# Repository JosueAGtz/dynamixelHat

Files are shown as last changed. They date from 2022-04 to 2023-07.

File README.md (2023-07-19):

# RaspberryPi Dynamixel Hat

The Raspberry Pi Zero Dynamixel Hat it's an easy to use hardware that allows you to connect and communicate with Dynamixel Servo Motors by using the Savage Electronics AX interface circuit, providing the half-duplex communication needed by these motors, its implemented in it a voltage converter for all the signals to the Raspberry allowing a secure communication in terms of logical levels.

It also implements a MAX25232ATCG/V+ which is a synchronous step-down DC-DC converter optimized for applications with high power density, This regulator will let you power your Raspberry directly from a battery and also provide power to your motors.

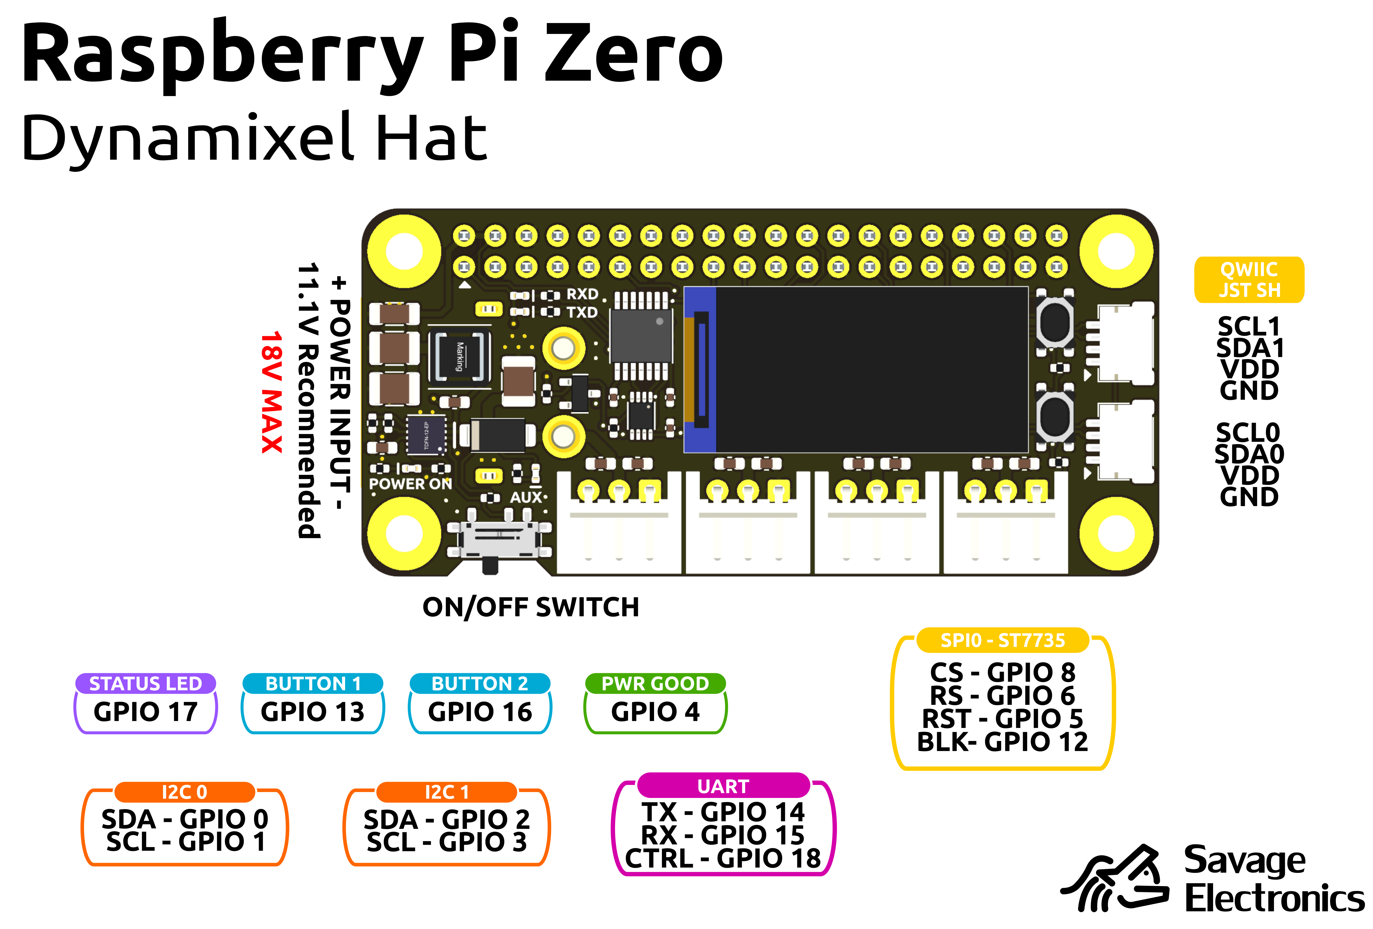
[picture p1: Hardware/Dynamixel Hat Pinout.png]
dynamixelHat


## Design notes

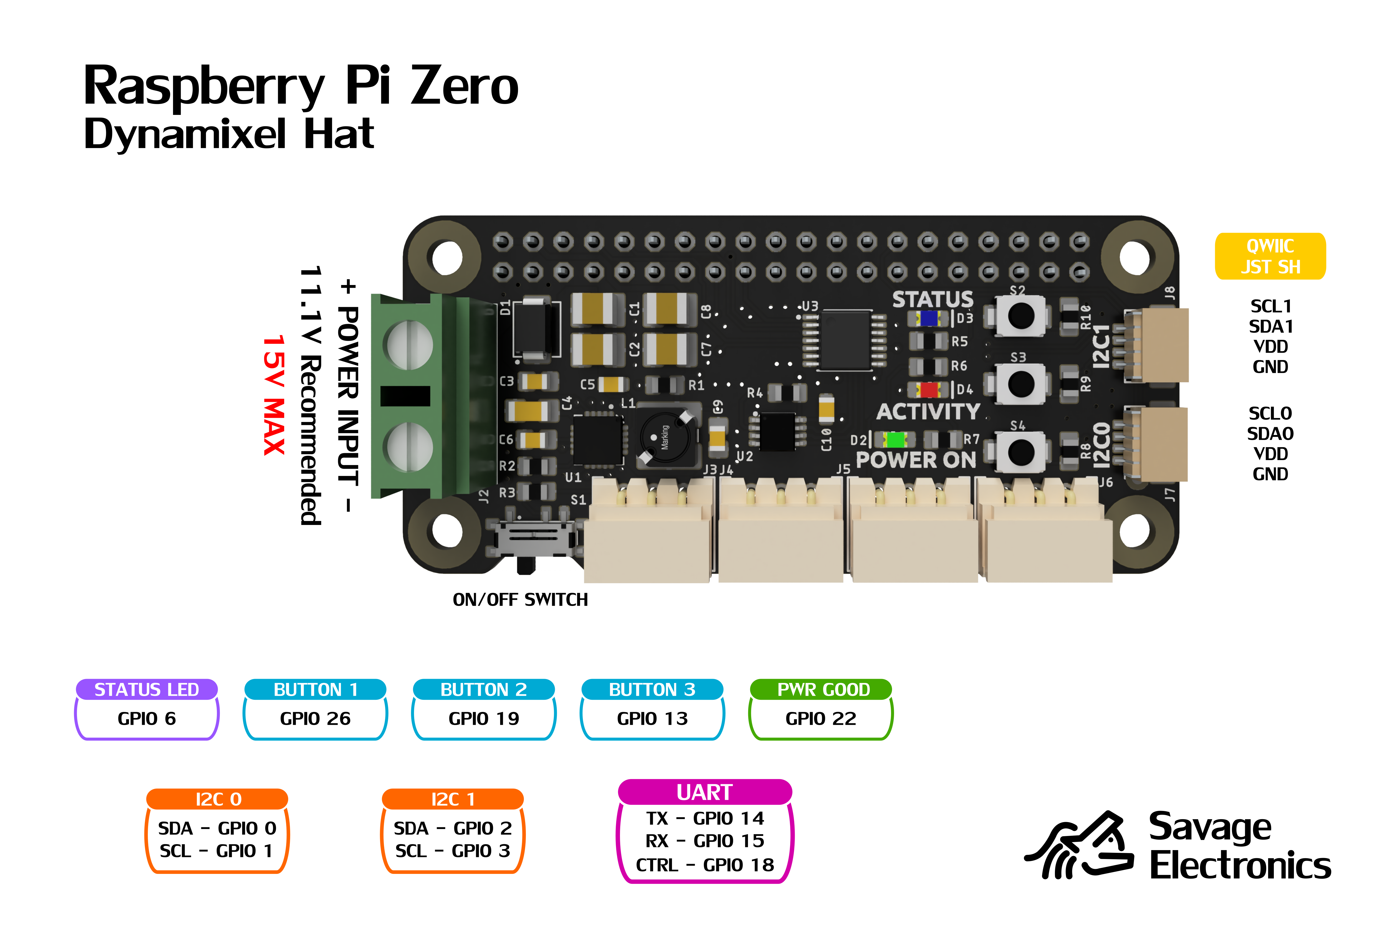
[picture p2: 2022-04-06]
Hardware/Dynamixel Hat Maxim Pinout.PNG

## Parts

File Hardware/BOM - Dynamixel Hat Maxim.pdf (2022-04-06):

# BOM - Raspberry Pi Zero Dinamixel Hat

# | Designator | Part Number | Description | Manufacturer | Distribuitor | Quantity

1 | J1 | 61304021821 | Headers & Wire Housings WR-PHD DUAL SCKT HDR 2.54mm | WE | MOUSER | 1
2 | J2 | 691137910002 | Pluggable Terminal Blocks WR-TBL 7.5mmPitch 2P Wire Protector | WE | MOUSER | 1
3 | D1 | B330B-13-F | Schottky Diodes & Rectifiers 30V 3A | Diodes Incorporated | MOUSER | 1
4 | C1,C2 | 885012209025 | Multilayer Ceramic Capacitors MLCC - SMD/SMT WCAP-CSGP 2.2uF 1210 10% 25V | WE | MOUSER | 2
5 | C3,C9 | 885012207072 | Multilayer Ceramic Capacitors MLCC - SMD/SMT WCAP-CSGP 0.1uF 0805 10% 25V | WE | MOUSER | 2
6 | C4 | 885012108019 | Multilayer Ceramic Capacitors MLCC - SMD/SMT WCAP-CSGP 2.2uF 1206 20% 25V | WE | MOUSER | 1
7 | C5 | 885012206071 | Multilayer Ceramic Capacitors MLCC - SMD/SMT WCAP-CSGP 0.1uF 0603 10% 25V | WE | MOUSER | 1
8 | C7,C8 | 885012109014 | Multilayer Ceramic Capacitors MLCC - SMD/SMT WCAP-CSGP 22uF 1210 20% 25V | WE | MOUSER | 2
9 | C6 | 885012207065 | Multilayer Ceramic Capacitors MLCC - SMD/SMT WCAP-CSGP 6800pF 0805 10% 25V | WE | MOUSER | 1
10 | U1 | MAX17633BATP+ | Switching Voltage Regulators 36V, 3.5A, High-Efficiency, Synchronous Step-Down DC-DC Converter | MAX | MOUSER | 1
11 | L1 | 74408942012 | Fixed Inductors WE-SPC SMD 4828 1.2uH 3.20A .022Ohm | WE | MOUSER | 1
12 | U2 | SN74LVC2G241DCTR | Buffers & Line Drivers Tri-State Dual | TI | MOUSER | 1
13 | U3 | TXB0104PWR | Translation - Voltage Levels 4-Bit Bi-directional V-Level Translator | TI | MOUSER | 1
14 | J3,J4,J5,J6 | 22-05-7035 | Headers & Wire Housings 3 CKT 2.5MM R/A HDR | Molex | MOUSER | 4
15 | J7,J8 | SM04B-SRSS-TB | CONNECTOR, HEADER, 1MM, 4 POSITION, 1ROW | JST | NEWARK | 2
16 | R1,R3,R4,R8,R9,R10 | ERJ-6GEYJ103V | Thick Film Resistors 0805 10Kohms 5% AEC-Q200 | Panasonic | MOUSER | 6
17 | R5,R6,R7 | ERJ-6GEYJ102V | Thick Film Resistors 0805 1Kohms 5% AEC-Q200 | Panasonic | MOUSER | 3
18 | R2 | ERJ-6GEYJ822V | Thick Film Resistors 0805 8.2Kohms 5% AEC-Q200 | Panasonic | MOUSER | 1
19 | D2 | 150080VS75000 | Standard LEDs - SMD WL-SMCW SMDMono TpVw Waterclr 0805 BrtGrn | WE | MOUSER | 1
20 | D3 | 150080SS75000 | Standard LEDs - SMD WL-SMCW SMDMono TpVw Waterclr 0805 SprRed | WE | MOUSER | 1
21 | D4 | 150080YS75000 | Standard LEDs - SMD WL-SMCW SMDMono TpVw Waterclr 0805 Yellow | WE | MOUSER | 1
22 | S1 | 450404015514 | Wurth Elektronik WS-SLSU Mini Slide Switch | WE | MOUSER | 1
23 | S2,S3,S4 | 434123025826 | Wurth Elektronik WS-TASV Tact Switch | WE | MOUSER | 3
24 | PCB | S/N | PCB Raspberry Pi Zero Dynamixel Hat | N/A | N/A | 1

### Optional

25 | Spacer | 970120365 | Standoffs & Spacers WA-SPaIE Spacer Stud M3x12mm SW 6 | WE | MOUSER | 4
26 | Screw | 97790603211 | Standoffs & Spacers WA-SCRW M3x6mm | WE | MOUSER | 8

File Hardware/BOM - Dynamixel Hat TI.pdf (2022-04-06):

# BOM - Raspberry Pi Zero Dynamixel Hat

# | Referencia | Numero de parte | Descripción | Fabricante | Distribuidor | Cantidad

1 | J1 | 61304021821 | Alojamientos de cables y cabecera WR-PHD DUAL SCKT HDR 2.54MM | WE | MOUSER | 1
2 | J2 | 691137910002 | Bloques de terminales fijas WR-TBL Terminal block - Wire protector - THT | WE | MOUSER | 1
3 | D1 | B330B-13-F | Rectificadores y diodos Schottky 30V 3A | Diodes Incorporated | MOUSER | 1
4 | C1 | 865080643007 | Capacitores electrolíticos de aluminio - SMD WCAP-ASLI 15uF 50V 20% SMD/SMT | WE | MOUSER | 1
5 | C2 | 865080643008 | Capacitores electrolíticos de aluminio - SMD WCAP-ASLI 22uF 50V 20% SMD/SMT | WE | MOUSER | 1
6 | U1 | TPS62143RGTR | Reguladores de voltaje de conmutación 3-17V 2A SD Cnvrtr | TI | MOUSER | 1
7 | L1 | 74406042022 | Inductores fijos WE-LQFS 4818 2.2uH 3.36A | WE | MOUSER | 1
8 | U2 | SN74LVC2G241DCTR | Búfers y controladores de línea Tri-State Dual | TI | MOUSER | 1
9 | U3 | TXB0104PWR | Traducción - Niveles de tensión 4-Bit Bi-directional V-Level Translator | TI | MOUSER | 1
10 | J3,J4,J5,J6 | 22-05-7035 | Alojamientos de cables y cabecera 3 CKT 2.5MM R/A HDR | Molex | MOUSER | 4
11 | J7,J8 | SM04B-SRSS-TB | CONNECTOR, HEADER, 1MM, 4 POSITION, 1ROW | JST | NEWARK | 2
12 | C3,C4,C5 | 885012207098 | Capacitores cerámicos (MLCC) - SMD/SMT WCAP-CSGP 0.1uF 0805 10% 50V MLCC | WE | MOUSER | 3
13 | R1,R2,R3,R7,R8,R9 | ERJ-6GEYJ103V | Thick Film Resistors 0805 10Kohms 5% AEC-Q200 | Panasonic | MOUSER | 6
14 | R4,R5,R6 | ERJ-6GEYJ102V | Thick Film Resistors 0805 1Kohms 5% AEC-Q200 | Panasonic | MOUSER | 3
15 | D2 | 150080VS75000 | LED estándar - SMD (montaje superficial) WL-SMCW SMDMono TpVw Waterclr 0805 BrtGrn | WE | MOUSER | 1
16 | D3 | 150080SS75000 | LED estándar - SMD (montaje superficial) WL-SMCW SMDMono TpVw Waterclr 0805 SprRed | WE | MOUSER | 1
17 | D4 | 150080YS75000 | LED estándar - SMD (montaje superficial) WL-SMCW SMDMono TpVw Waterclr 0805 Yellow | WE | MOUSER | 1
18 | S1 | 450404015514 | Wurth Elektronik WS-SLSU Mini Slide Switch | WE | MOUSER | 1
19 | S2,S3,S4 | 434123025826 | Wurth Elektronik WS-TASV Tact Switch | WE | MOUSER | 3
20 | PCB | S/N | PCB Raspberry Pi Zero Dynamixel Hat | N/A | N/A | 1

Optional

21 | Spacer | 970120365 | Standoffs & Spacers WA-SPaIE Spacer Stud M3x12mm SW 6 | WE | MOUSER | 4
22 | Screw | 97790603211 | Standoffs & Spacers WA-SCRW M3x6mm | WE | MOUSER | 8

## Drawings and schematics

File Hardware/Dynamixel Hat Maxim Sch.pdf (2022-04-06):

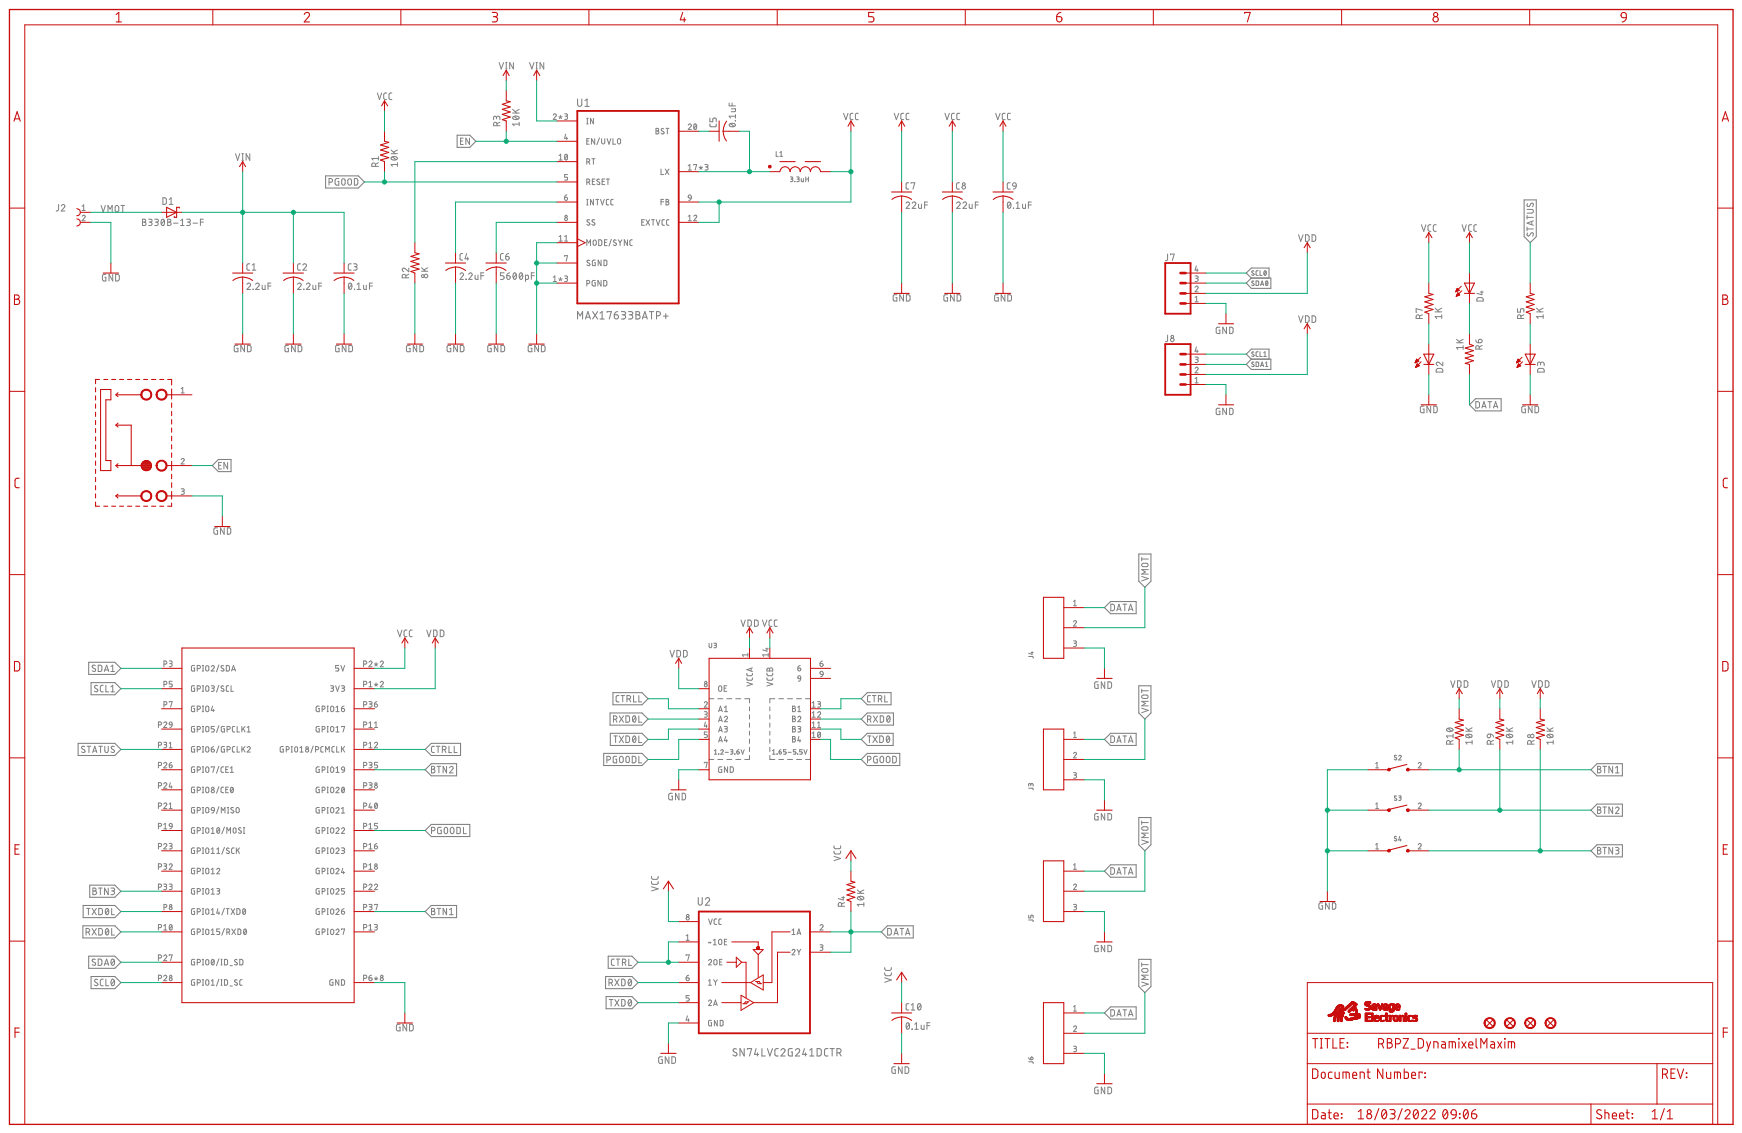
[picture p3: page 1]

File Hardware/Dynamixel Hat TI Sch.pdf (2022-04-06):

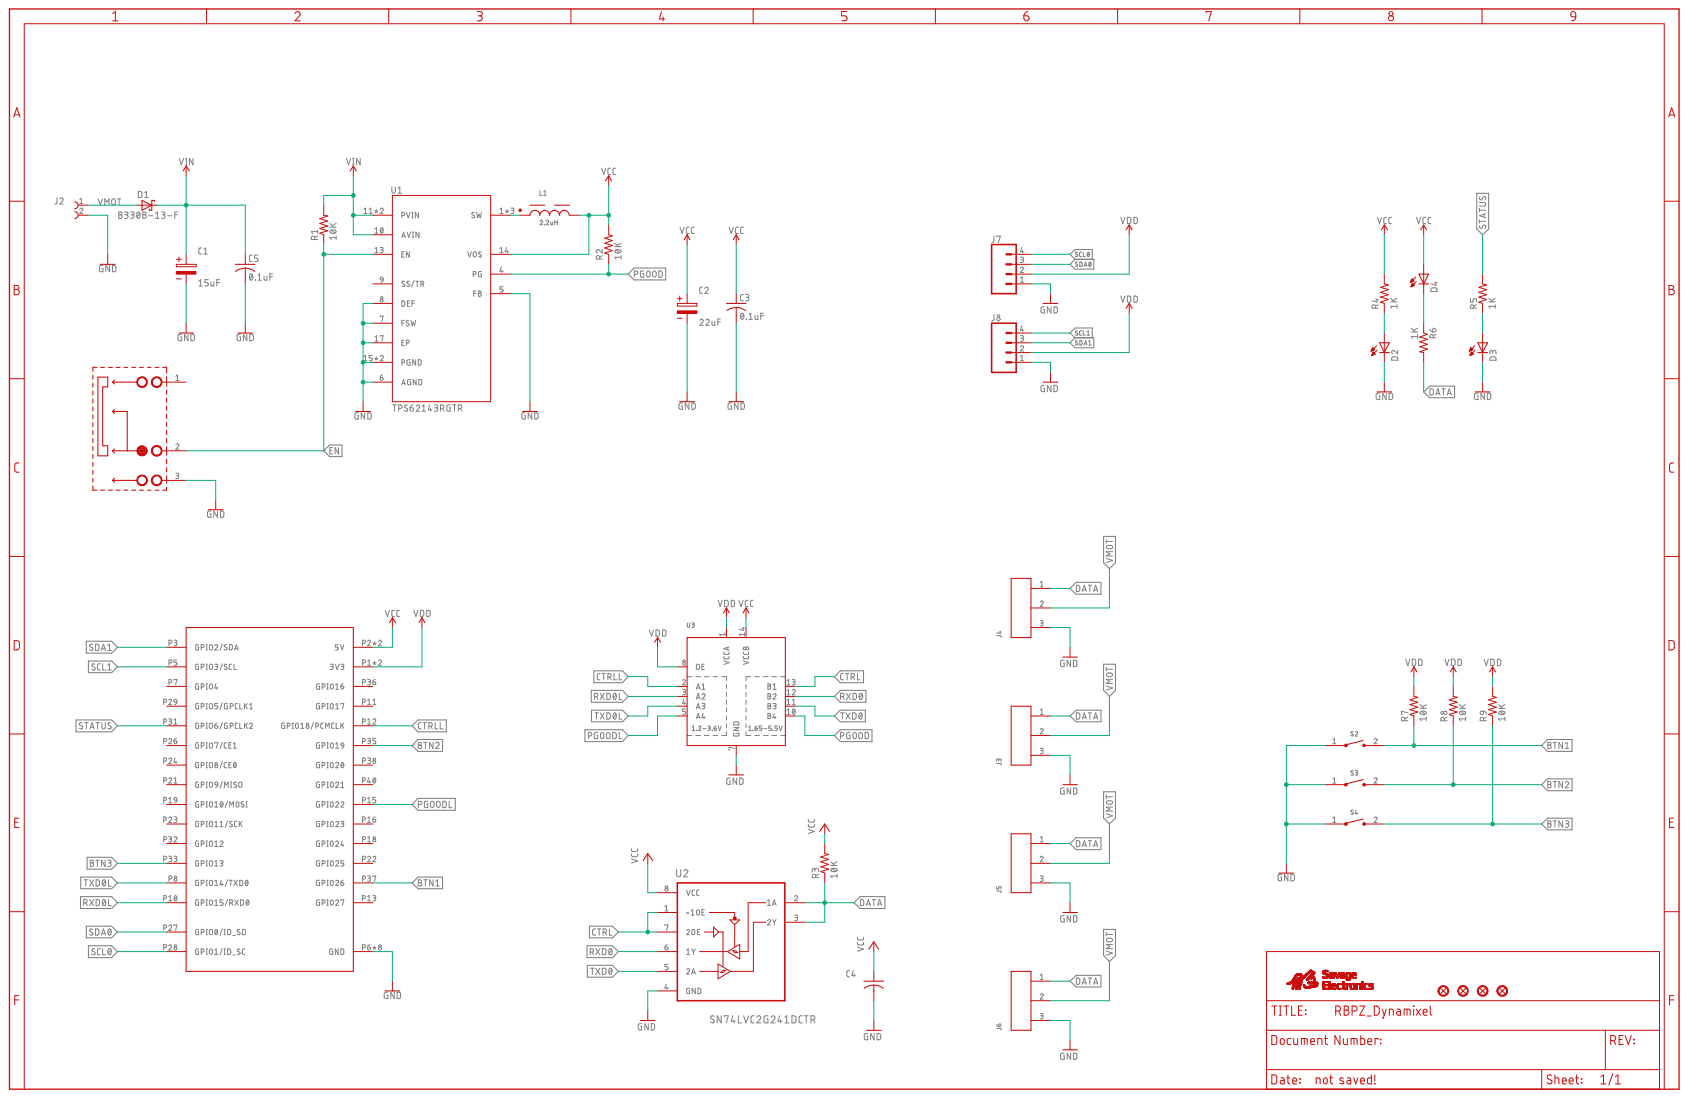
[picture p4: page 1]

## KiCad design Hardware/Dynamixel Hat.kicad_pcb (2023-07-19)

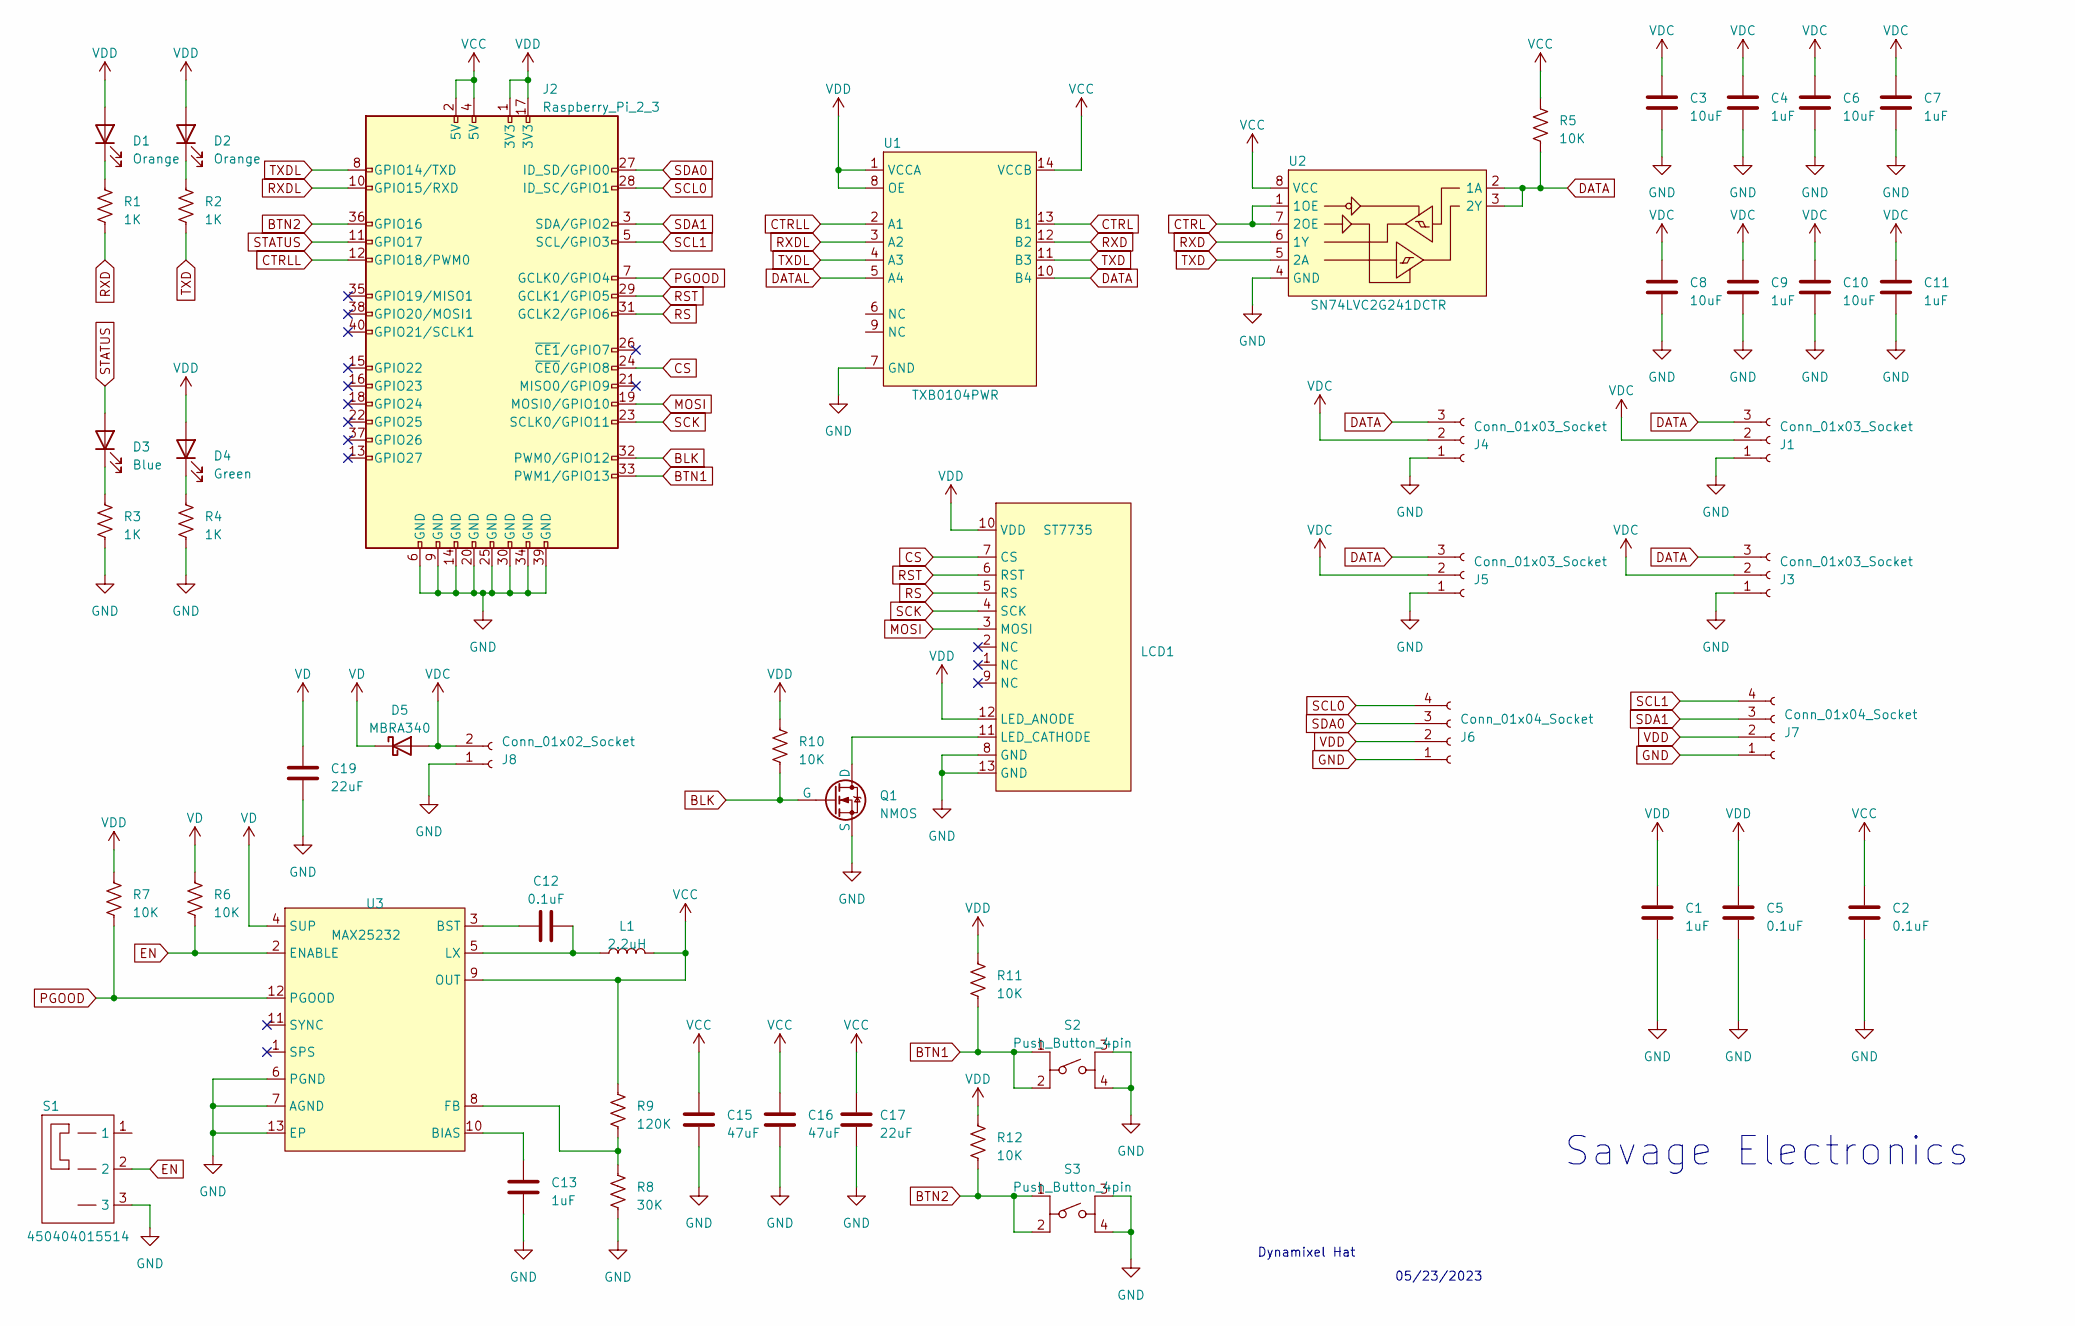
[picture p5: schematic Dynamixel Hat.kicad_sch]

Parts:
C1: 1uF; C_0402_1005Metric
C2, C5: 0.1uF; C_0402_1005Metric
C3, C6, C8, C10: 10uF; C_0603_1608Metric
C4, C7, C9, C11, C13: 1uF; C_0603_1608Metric
C12: 0.1uF; C_0603_1608Metric
C15, C16: 47uF; C_1210_3225Metric
C17: 22uF; C_1206_3216Metric
C19: 22uF; C_1210_3225Metric
D1, D2: Orange; 0402LED
D3: Blue; 0402LED
D4: Green; 0402LED
D5: MBRA340; D_SMA
J1, J3, J4, J5: Conn_01x03_Socket; JST_EH_S3B-EH_1x03_P2.50mm_Horizontal
J2: Raspberry_Pi_2_3; Raspberry Pi Zero Hat
J6, J7: Conn_01x04_Socket; JST_SH_SM04B-SRSS-TB_1x04-1MP_P1.00mm_Horizontal
J8: Conn_01x02_Socket; XT60PW-M20
L1: 2.2uH; L_Taiyo-Yuden_MD-5050
LCD1: ST7735; IPS 0.96
Q1: NMOS; SOT-23
R1, R2, R3, R4: 1K; R_0402_1005Metric
R5, R6, R7, R10, R11, R12: 10K; R_0402_1005Metric
R8: 30K; R_0402_1005Metric
R9: 120K; R_0402_1005Metric
S1: 450404015514; 450404015514_SW
S2, S3: Push_Button_4pin; 434123025826
U1: TXB0104PWR; TSSOP14_5x4.4_0.65
U2: SN74LVC2G241DCTR; VSSOP-8_2.3x2mm_P0.5mm
U3: MAX25232; TDFN12_3x3mm_P05_EP

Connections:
BLK: J2.32 (PWM0/GPIO12), Q1.1 (G), R10.2
BTN1: J2.33 (PWM1/GPIO13), R11.2, S2.1, S2.2
BTN2: J2.36 (GPIO16), R12.2, S3.1, S3.2
CS: J2.24 (~CE0/GPIO8), LCD1.7 (CS)
CTRL: U1.13 (B1), U2.1 (1OE), U2.7 (2OE)
CTRLL: J2.12 (GPIO18/PWM0), U1.2 (A1)
DATA: J1.3, J3.3, J4.3, J5.3, R5.2, U1.10 (B4), U2.2 (1A), U2.3 (2Y)
DATAL: U1.5 (A4)
EN: R6.2, S1.2, U3.2 (ENABLE)
GND: C1.2, C2.2, C3.2, C4.2, C5.2, C6.2, C7.2, C8.2, C9.2, C10.2, C11.2, C13.2, C15.2, C16.2, C17.2, C19.2, J1.1, J2.6 (GND), J2.9 (GND), J2.14 (GND), J2.20 (GND), J2.25 (GND), J2.30 (GND), J2.34 (GND), J2.39 (GND), J3.1, J4.1, J5.1, J6.1, J7.1, J8.1, LCD1.8 (GND), LCD1.13 (GND), Q1.2 (S), R3.2, R4.2, R8.2, S1.3, S2.3, S2.4, S3.3, S3.4, U1.7 (GND), U2.4 (GND), U3.6 (PGND), U3.7 (AGND), U3.13 (EP)
MOSI: J2.19 (MOSI0/GPIO10), LCD1.3 (MOSI)
unnamed: D1.1 (K), R1.1
unnamed: D2.1 (K), R2.1
unnamed: D3.1 (K), R3.1
unnamed: D4.1 (K), R4.1
unnamed: LCD1.11 (LED_CATHODE), Q1.3 (D)
unnamed: C13.1, U3.10 (BIAS)
unnamed: C12.1, U3.3 (BST)
unnamed: R8.1, R9.2, U3.8 (FB)
unnamed: C12.2, L1.1, U3.5 (LX)
PGOOD: J2.7 (GCLK0/GPIO4), R7.2, U3.12 (PGOOD)
RS: J2.31 (GCLK2/GPIO6), LCD1.5 (RS)
RST: J2.29 (GCLK1/GPIO5), LCD1.6 (RST)
RXD: R1.2, U1.12 (B2), U2.6 (1Y)
RXDL: J2.10 (GPIO15/RXD), U1.3 (A2)
SCK: J2.23 (SCLK0/GPIO11), LCD1.4 (SCK)
SCL0: J2.28 (ID_SC/GPIO1), J6.4
SCL1: J2.5 (SCL/GPIO3), J7.4
SDA0: J2.27 (ID_SD/GPIO0), J6.3
SDA1: J2.3 (SDA/GPIO2), J7.3
STATUS: D3.2 (A), J2.11 (GPIO17)
TXD: R2.2, U1.11 (B3), U2.5 (2A)
TXDL: J2.8 (GPIO14/TXD), U1.4 (A3)
VCC: C2.1, C15.1, C16.1, C17.1, J2.2 (5V), J2.4 (5V), L1.2, R5.1, R9.1, U1.14 (VCCB), U2.8 (VCC), U3.9 (OUT)
VD: C19.1, D5.1 (K), R6.1, U3.4 (SUP)
VDC: C3.1, C4.1, C6.1, C7.1, C8.1, C9.1, C10.1, C11.1, D5.2 (A), J1.2, J3.2, J4.2, J5.2, J8.2
VDD: C1.1, C5.1, D1.2 (A), D2.2 (A), D4.2 (A), J2.1 (3V3), J2.17 (3V3), J6.2, J7.2, LCD1.10 (VDD), LCD1.12 (LED_ANODE), R7.1, R10.1, R11.1, R12.1, U1.1 (VCCA), U1.8 (OE)

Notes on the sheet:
Dynamixel Hat
05/23/2023
Savage Electronics

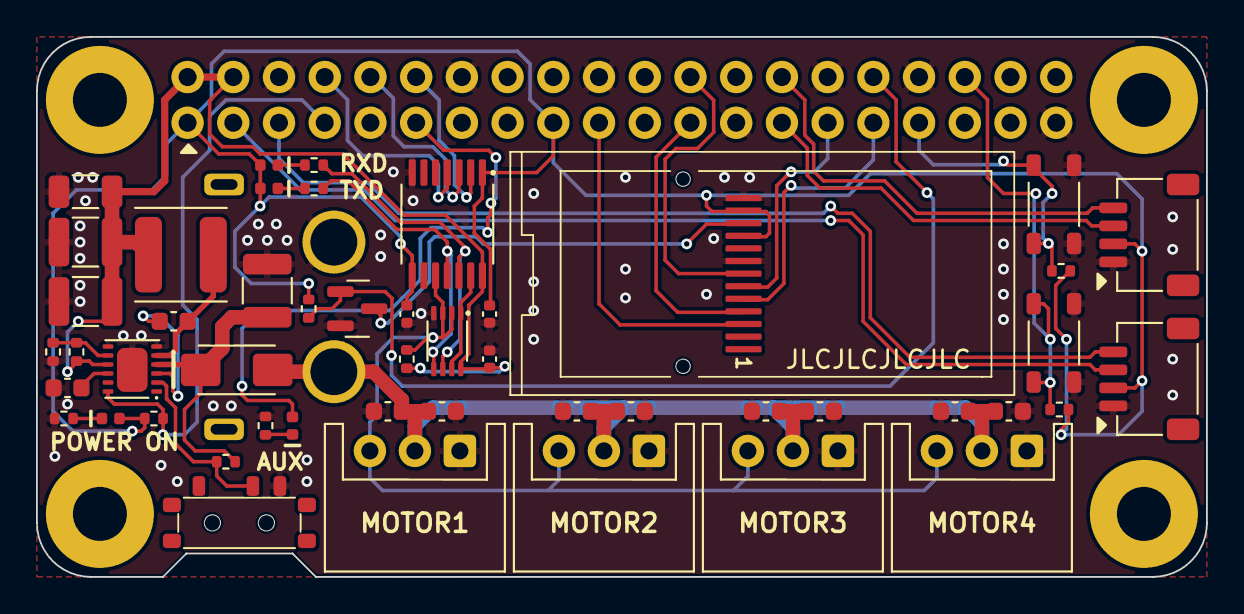
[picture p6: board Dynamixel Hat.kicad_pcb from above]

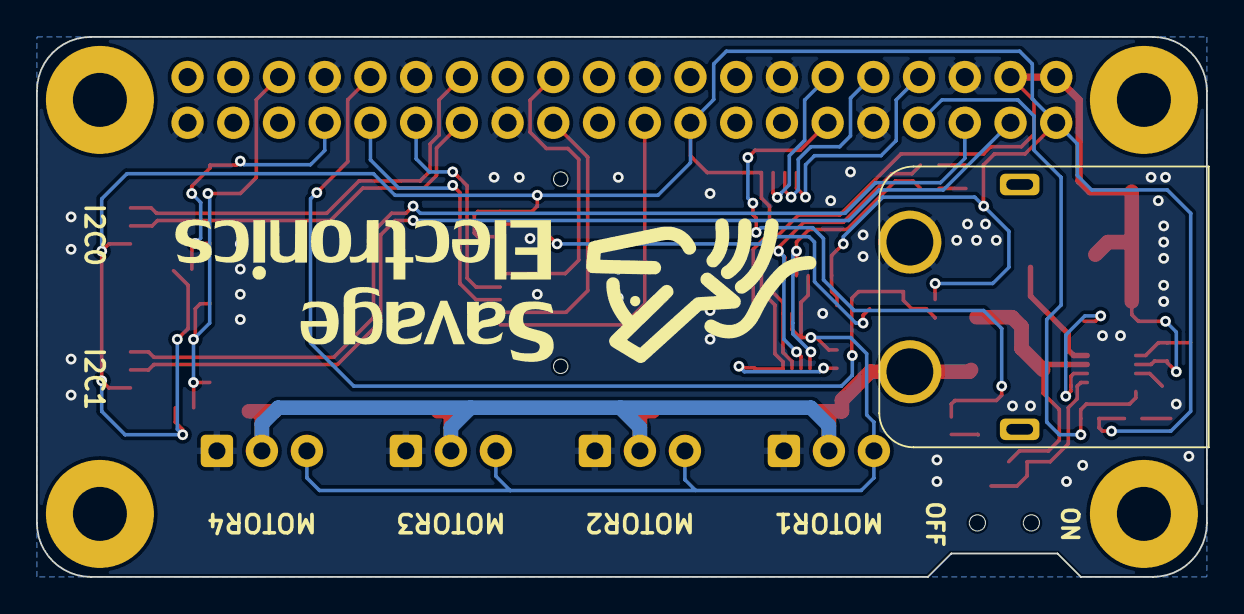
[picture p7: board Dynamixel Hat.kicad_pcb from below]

Board: 2 copper layers, 65.0 x 30.0 mm, 52 parts (2 on the bottom side), 36 nets.

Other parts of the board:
G_logoMedium: LOGO; G_SELOGO_MED

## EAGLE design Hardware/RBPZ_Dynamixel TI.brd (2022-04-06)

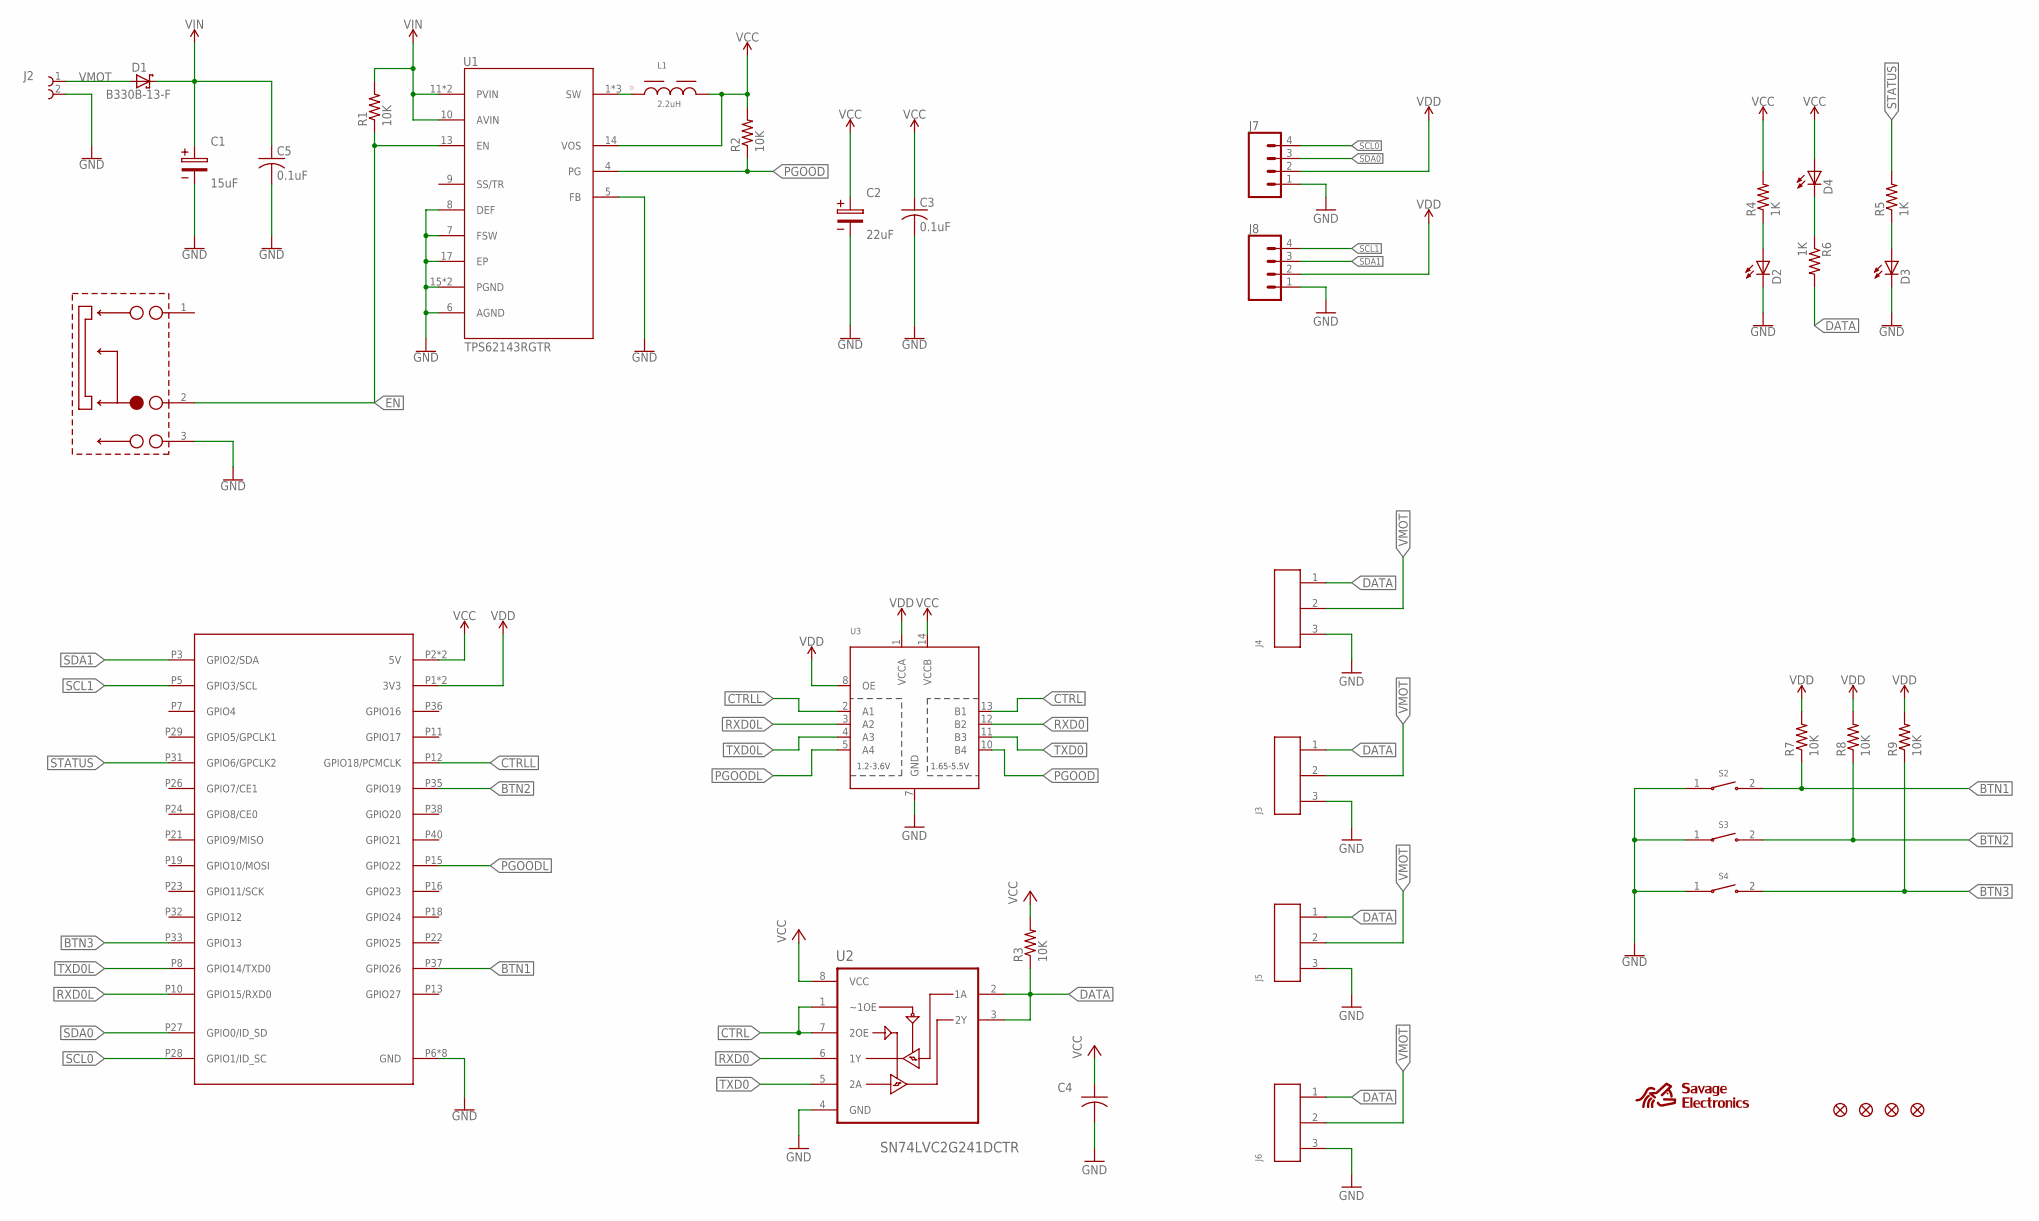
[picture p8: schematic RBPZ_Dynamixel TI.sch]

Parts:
C1: 15uF; 3.5X1.6X2.1(BXCXA)
C2: 22uF; 3.5X1.6X2.1(BXCXA)
C3, C5: 0.1uF; C0805
C4: 1uF; C0805
D1: B330B-13-F; DIONM4336X250N
D2, D3, D4: LEDCHIP-LED0805; CHIP-LED0805
FID1, FID2, FID3, FID4: FIDUCIAL""; FIDUCIAL_1MM
J1: RBPZERO; 61004021821_RASPBERRYPIZERO
J2: 691137910002
J3, J4, J5, J6: 64600311622
J7, J8: CONN_04SMD2; 1X04_1MM_RA
L1: 2.2uH; WE-LQFS_48X8
R1, R2, R3, R7, R8, R9: 10K; R0805
R4, R5, R6: 1K; R0805
S1: 450404015514
S2, S3, S4: 434123025826-2PIN
U1: TPS62143RGTR; QFN50P300X300X80-17N
U2: SN74LVC2G241DCTR; SOP65P400X130-8N
U3: TXB0104PWR; TSSOP14

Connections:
BTN1: J1.P37 (GPIO26), R7.1, S2.2
BTN2: J1.P35 (GPIO19), R8.1, S3.2
BTN3: J1.P33 (GPIO13), R9.1, S4.2
CTRL: U2.1 (~1OE), U2.7 (2OE), U3.13 (B1)
CTRLL: J1.P12 (GPIO18/PCMCLK), U3.2 (A1)
DATA: J3.1, J4.1, J5.1, J6.1, R3.1, R6.2, U2.2 (1A), U2.3 (2Y)
EN: R1.1, S1.2, U1.13 (EN)
GND: C1.2, C2.2, C3.2, C4.2, C5.2, D2.C, D3.C, J1.P6 (GND), J1.P9 (GND), J1.P14 (GND), J1.P20 (GND), J1.P25 (GND), J1.P30 (GND), J1.P34 (GND), J1.P39 (GND), J2.2, J3.3, J4.3, J5.3, J6.3, J7.1, J8.1, S1.3, S2.1, S3.1, S4.1, U1.5 (FB), U1.6 (AGND), U1.7 (FSW), U1.8 (DEF), U1.15 (PGND), U1.16 (PGND), U1.17 (EP), U2.4 (GND), U3.7 (GND)
unnamed: D4.C, R6.1
unnamed: D2.A, R4.1
unnamed: L1.1, U1.1 (SW), U1.2 (SW), U1.3 (SW)
unnamed: D3.A, R5.1
PGOOD: R2.1, U1.4 (PG), U3.10 (B4)
PGOODL: J1.P15 (GPIO22), U3.5 (A4)
RXD0: U2.6 (1Y), U3.12 (B2)
RXD0L: J1.P10 (GPIO15/RXD0), U3.3 (A2)
SCL0: J1.P28 (GPIO1/ID_SC), J7.4
SCL1: J1.P5 (GPIO3/SCL), J8.4
SDA0: J1.P27 (GPIO0/ID_SD), J7.3
SDA1: J1.P3 (GPIO2/SDA), J8.3
STATUS: J1.P31 (GPIO6/GPCLK2), R5.2
TXD0: U2.5 (2A), U3.11 (B3)
TXD0L: J1.P8 (GPIO14/TXD0), U3.4 (A3)
VCC: C2.1, C3.1, C4.1, D4.A, J1.P2 (5V), J1.P4 (5V), L1.2, R2.2, R3.2, R4.2, U1.14 (VOS), U2.8 (VCC), U3.14 (VCCB)
VDD: J1.P1 (3V3), J1.P17 (3V3), J7.2, J8.2, R7.2, R8.2, R9.2, U3.1 (VCCA), U3.8 (OE)
VIN: C1.1, C5.1, D1.1 (C), R1.2, U1.10 (AVIN), U1.11 (PVIN), U1.12 (PVIN)
VMOT: D1.2 (A), J2.1, J3.2, J4.2, J5.2, J6.2

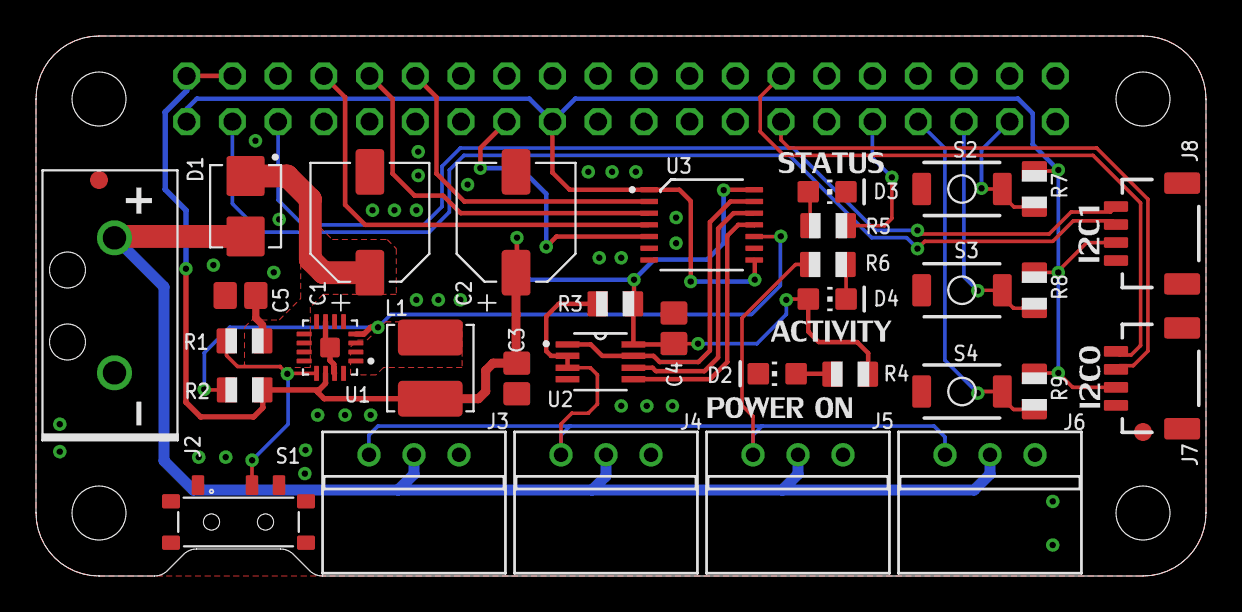
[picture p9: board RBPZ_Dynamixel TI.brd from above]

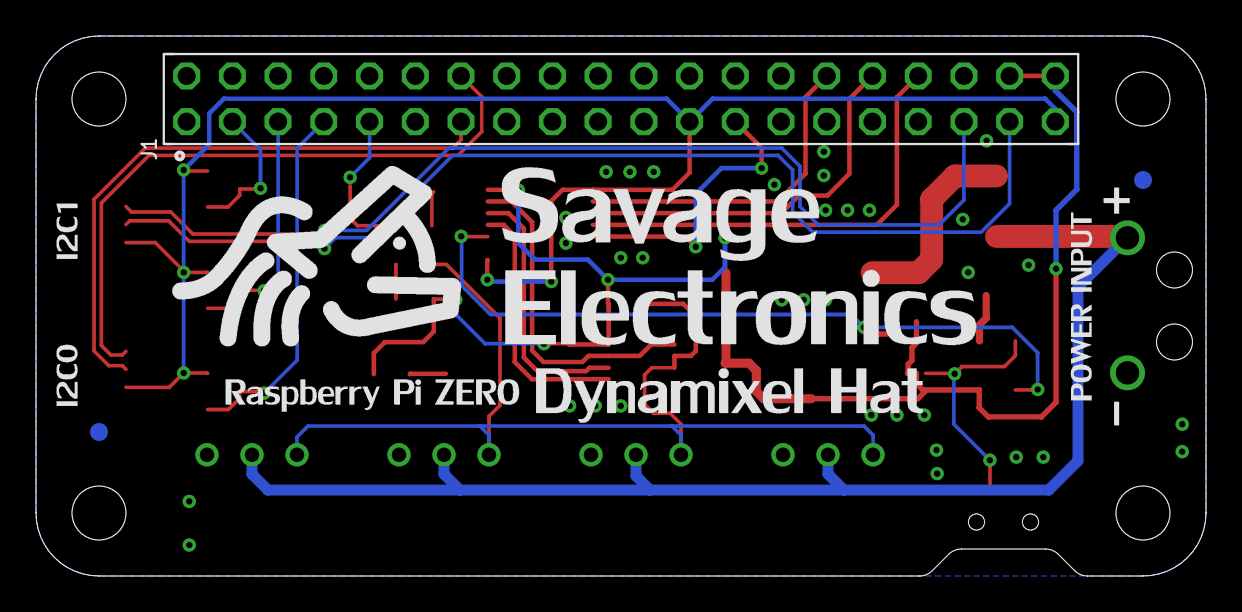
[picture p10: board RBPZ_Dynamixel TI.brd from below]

Board: 2 copper layers, 65.0 x 30.0 mm, 38 parts (3 on the bottom side), 27 nets.

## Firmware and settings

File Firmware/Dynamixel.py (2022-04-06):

import RPi.GPIO as GPIO
import serial
import time

GPIO.setwarnings(False)
GPIO.setmode(GPIO.BCM)
GPIO.setup(18,GPIO.OUT)     # Control Data Direction Pin
GPIO.setup(6,GPIO.OUT)      # Blue LED Pin

GPIO.setup(26,GPIO.IN)      # S2 Push Button Pin
GPIO.setup(19,GPIO.IN)      # S3 Push Button Pin
GPIO.setup(13,GPIO.IN)      # S4 Push Button Pin


Dynamixel=serial.Serial("/dev/ttyS0",baudrate=1000000,timeout=0.1, bytesize=8)   # UART in ttyS0 @ 1Mbps


while True:

    if GPIO.input(26):
        GPIO.output(6,GPIO.LOW)
    else:
        GPIO.output(6,GPIO.HIGH)
        GPIO.output(18,GPIO.HIGH)
        Dynamixel.write(bytearray.fromhex("FF FF 01 05 03 1E CD 00 0B"))  # Move Servo with ID = 1 to position 205
        GPIO.output(18,GPIO.LOW)
        startDynamixel = Dynamixel.read()
        startDynamixel = Dynamixel.read()
        idDynamixel = Dynamixel.read()
        lenghtDynamixel = Dynamixel.read()
        errorDynamixel = Dynamixel.read()
        chkDynamixel = Dynamixel.read()
        print("Servo ID = " , int.from_bytes(idDynamixel,byteorder='big') , " Errors = ", int.from_bytes(errorDynamixel,byteorder='big'))
        time.sleep(1)

    if GPIO.input(19):
        GPIO.output(6,GPIO.LOW)
    else:
        GPIO.output(6,GPIO.HIGH)
        GPIO.output(18,GPIO.HIGH)
        Dynamixel.write(bytearray.fromhex("FF FF 01 04 02 2A 01 CD"))   # Read Voltage of Servo with ID = 1 
        GPIO.output(18,GPIO.LOW)
        startDynamixel = Dynamixel.read()
        startDynamixel = Dynamixel.read()
        idDynamixel = Dynamixel.read()
        lenghtDynamixel = Dynamixel.read()
        errorDynamixel = Dynamixel.read()
        voltDynamixel = Dynamixel.read()
        chkDynamixel = Dynamixel.read()
        print("Servo Voltage = " , int.from_bytes(voltDynamixel,byteorder='big'))
        GPIO.output(18,GPIO.HIGH)
        Dynamixel.write(bytearray.fromhex("FF FF 01 04 02 2B 01 CC"))   # Read Temperature of Servo with ID = 1
        GPIO.output(18,GPIO.LOW)
        startDynamixel = Dynamixel.read()
        startDynamixel = Dynamixel.read()
        idDynamixel = Dynamixel.read()
        lenghtDynamixel = Dynamixel.read()
        errorDynamixel = Dynamixel.read()
        tempDynamixel = Dynamixel.read()
        chkDynamixel = Dynamixel.read()
        print("Servo Temperature = " , int.from_bytes(tempDynamixel,byteorder='big'))
        GPIO.output(18,GPIO.HIGH)
        Dynamixel.write(bytearray.fromhex("FF FF 01 04 02 24 02 D2"))   # Read Position of Servo with ID = 1
        GPIO.output(18,GPIO.LOW)
        startDynamixel = Dynamixel.read()
        startDynamixel = Dynamixel.read()
        idDynamixel = Dynamixel.read()
        lenghtDynamixel = Dynamixel.read()
        errorDynamixel = Dynamixel.read()
        posDynamixel = Dynamixel.read(2)
        chkDynamixel = Dynamixel.read()
        print("Servo Position = " , int.from_bytes(posDynamixel,byteorder='little'))
        time.sleep(1)

    if GPIO.input(13):
        GPIO.output(6,GPIO.LOW)
    else:
        GPIO.output(6,GPIO.HIGH)
        GPIO.output(18,GPIO.HIGH)
        Dynamixel.write(bytearray.fromhex("FF FF 01 05 03 1E 32 03 A3"))    # Move Servo with ID = 1 to position 816
        GPIO.output(18,GPIO.LOW)
        startDynamixel = Dynamixel.read()
        startDynamixel = Dynamixel.read()
        idDynamixel = Dynamixel.read()
        lenghtDynamixel = Dynamixel.read()
        errorDynamixel = Dynamixel.read()
        chkDynamixel = Dynamixel.read()
        print("Servo ID = " , int.from_bytes(idDynamixel,byteorder='big') , " Errors = ", int.from_bytes(errorDynamixel,byteorder='big'))
        time.sleep(1)

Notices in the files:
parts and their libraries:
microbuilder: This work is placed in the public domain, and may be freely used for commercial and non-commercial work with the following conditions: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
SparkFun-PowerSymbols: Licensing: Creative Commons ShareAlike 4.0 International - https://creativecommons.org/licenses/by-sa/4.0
